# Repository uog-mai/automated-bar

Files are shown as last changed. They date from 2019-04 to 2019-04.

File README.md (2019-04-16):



 

<p align="center">
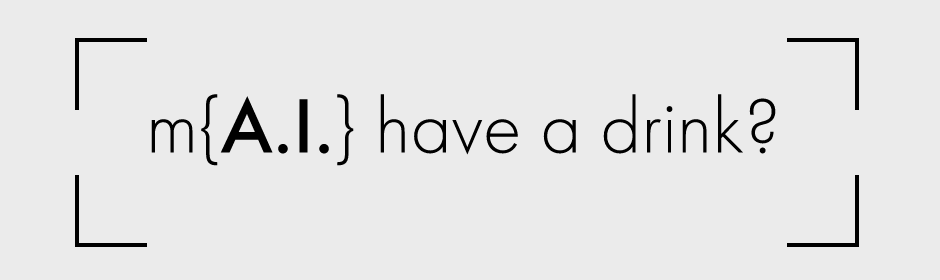
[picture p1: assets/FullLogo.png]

</p>

# m{A.I.} get you a drink?

m{A.I.} is a project aiming to produce a low-cost, voice-activated, automated drinks vending system for use in high-end consumer and commercial applications. Order your favourite drink through voice commands on Google Home on your mobile or use our custom made GUI to select drinks. 

This page will show you exactly how to build your own automated-bar for under £75, providing you with a components list, all the necessary CAD technical drawings and electronics schematics and an easy one step install for all the required software and firmware. 

Check out our design and build process on our Instagram page: [m{A.I.}.](https://www.instagram.com/m_a.i._/?hl=en)

Or our instructables for our full build instructions visit our [Instructables](https://www.instructables.com/id/Automated-Bar/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)

Completed as part of the University of Glasgow's Real Time Embedded Programming 5 team project

<p align="center">
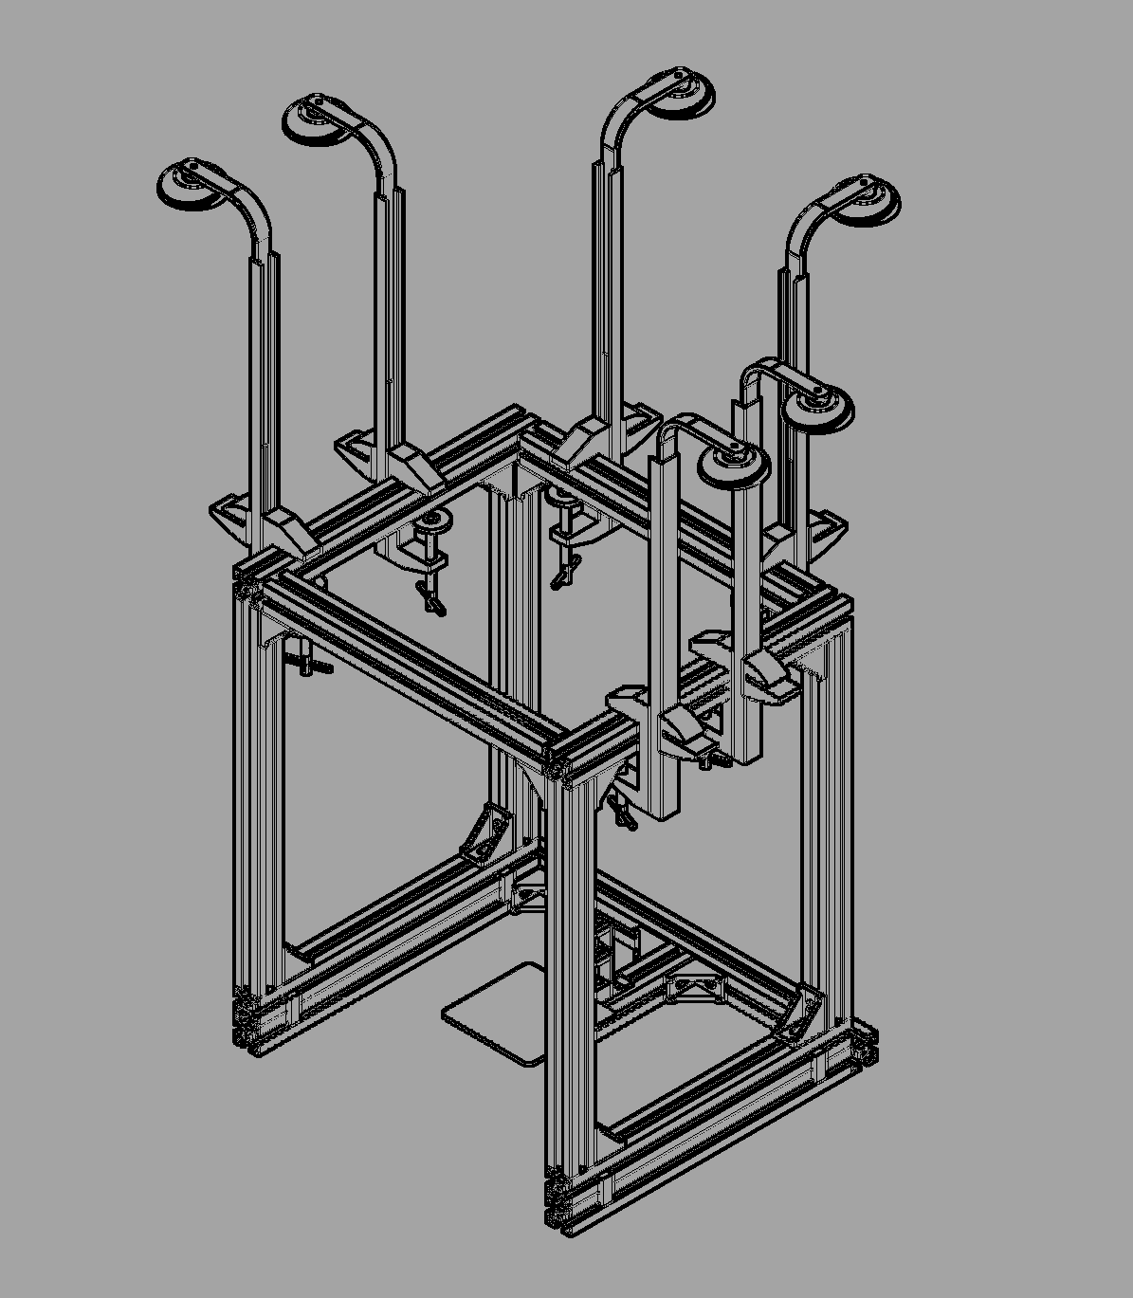
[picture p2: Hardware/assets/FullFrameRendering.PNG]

</p>

<p align="center">
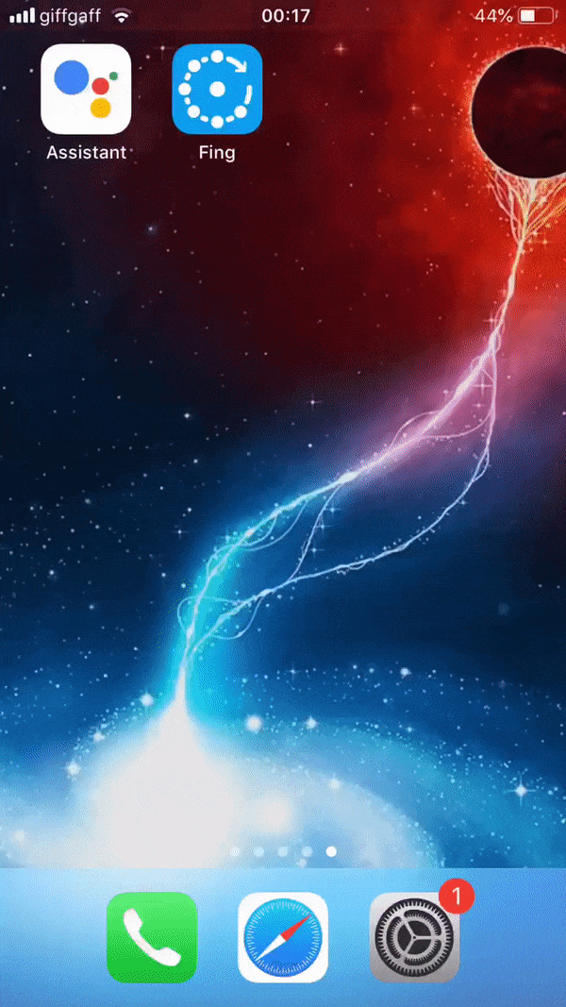
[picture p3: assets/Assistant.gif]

</p>
 
## Features
Scalability to any assortment of spirits and mixers

Google API integration for voice ordering

Extensive crawled database of recipes

Based on a Raspberry Pi 3 Model B

Low-cost aluminium extrusion structure

3D printed PLA fixtures

9g servo actuators

## Usage and Install Instructions
To use [dialogflow](https://dialogflow.com/) you must create a free account and import the ```CocktailRecipeBot``` which can be download from the software directory ```automated-bar/Software/dialogflow```. Download, unzip and upload it to dialogflow to begin use.

You will also need to sign-up and download [```ngrok```](https://dashboard.ngrok.com/user/signup) a secure traffic rerouting service for webhooks. This is needed to connect the dialogflow webhook to the Python server. This should be done on the Raspberry Pi.

This following software has only been verified to compile on the Raspberry Pi 3 Model B ```raspian (stretch)``` and ```Ubuntu 16.04```, however it should work on other raspbian distros and RPI models too.

This installation should be run from the command line of the Raspberry Pi by first cloning this git repo.
```bash
git clone https://github.com/uog-mai/automated-bar/
cd automated-bar/Software/
sudo source build.sh
```
This will download, install and compile all dependencies and the source code for the project.

Once installed, run the following in the ```ngrok``` install directory:
```bash
sudo ./ngrok http 5000
```
This will redirect a dynamically generated URL to your RPI. Where it says:
```Forwarding                    https://yourURL.ngrok.io``` copy the URL (makes sure its https *not* http). In the ``CocktailRecipeBot`` dialogflow on the left hand side where it says ```Fulfillment```, enable the webhook option and paste the ngrok URL.

Now navigate to the server folder inside the software directory, ```automated-bar/Software/Server``` and run:
```bash
python3 index.py
``` 
This should run your webserver (default traffic input through port 5000) on the RPI with the C++ shared object imported as a module. 

*Congratulations* You have completed the software set-up, you can now ask Google Home to talk to ```m{A.I.}``` (through voice or text) and you can begin ordering your drinks. 

## Overview
The automated bar holds an array of alcoholic drinks and mixers of the users choice, clamped onto the top of the frame, each paired with their own mounted servos. When a user orders a drink the volume and weight of the desired drink is found and calculated, and the appropriate servos are driven to dispsense the fluid the correct beverage. A proximity sensor on the cup stand checks whether a user has added a cup and a weight sensor confirms the correct amount of fluid has been dispensed. 

### Hardware 

#### Links

Full CAD resources including Autodesk Inventor files and assemblies of the system can be found within our Hardware subsection, and full electronics design files are available through the [Altium CircuitMaker community.](https://circuitmaker.com/Projects/Details/Peter-Fleming-2/UoG-mai-automated-bar) 

For full build instructions and BOM please see our Instructables page [here](https://www.instructables.com/id/Automated-Bar/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)

### Software
The software is split up into two sections: ```C++``` firmware and logic and and a ```Python``` web server that interacts with dialogflow. The logic section interacts with the firmware of the sensors and controls the handling of the fluid and the verificaiton of states. The Python web server acts to parse and network information from dialogflow to the logic.

<p align="center">
<img src="https://github.com/uog-mai/automated-bar/blob/develop/assets/InteractionDiagram.png" ">
</p>

Further details of the software can be found in the Software directory README: ```automated-bar/Software/README```and in the Software section of the Wiki.

## Contributors
[Peter Fleming](https://github.com/petemfleming)

[Joseph Marsden](https://github.com/jrmars)

[Edward Mortimer](https://github.com/eddymj96)

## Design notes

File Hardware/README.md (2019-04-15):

# Hardware Design

## Mechanical Build
The system was modelled in Autodesk Inventor Professional and comprised of aluminium extrusion and fixtures, COTS optics 
with rail mounts, and custom designed 3D printed PLA components. 
### Manufactured frame
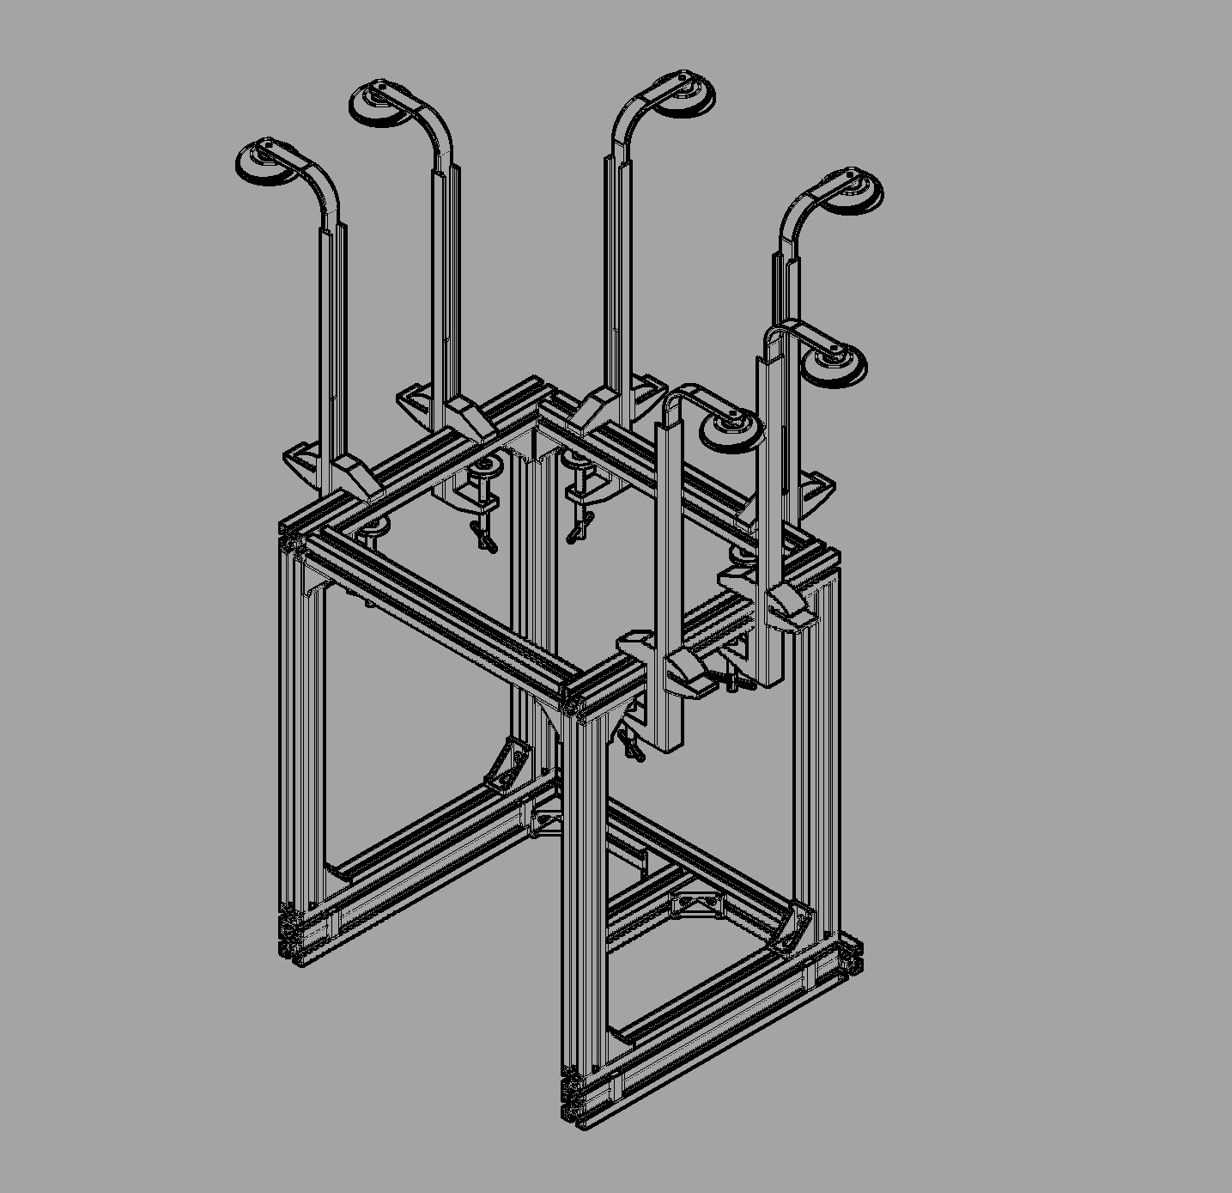
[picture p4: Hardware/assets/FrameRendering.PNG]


The dispensing systems operates through a 9g servo mounted on each optic, with a metal strut connecting it to the base of the 
plunger. As the servo rotates, the plunger mechanism is pulled upwards, closing the fill-line to the bottle, opening the 
dispenser line, and allowing air return via a sprung element within the optic.

### Optic dispensing assembly
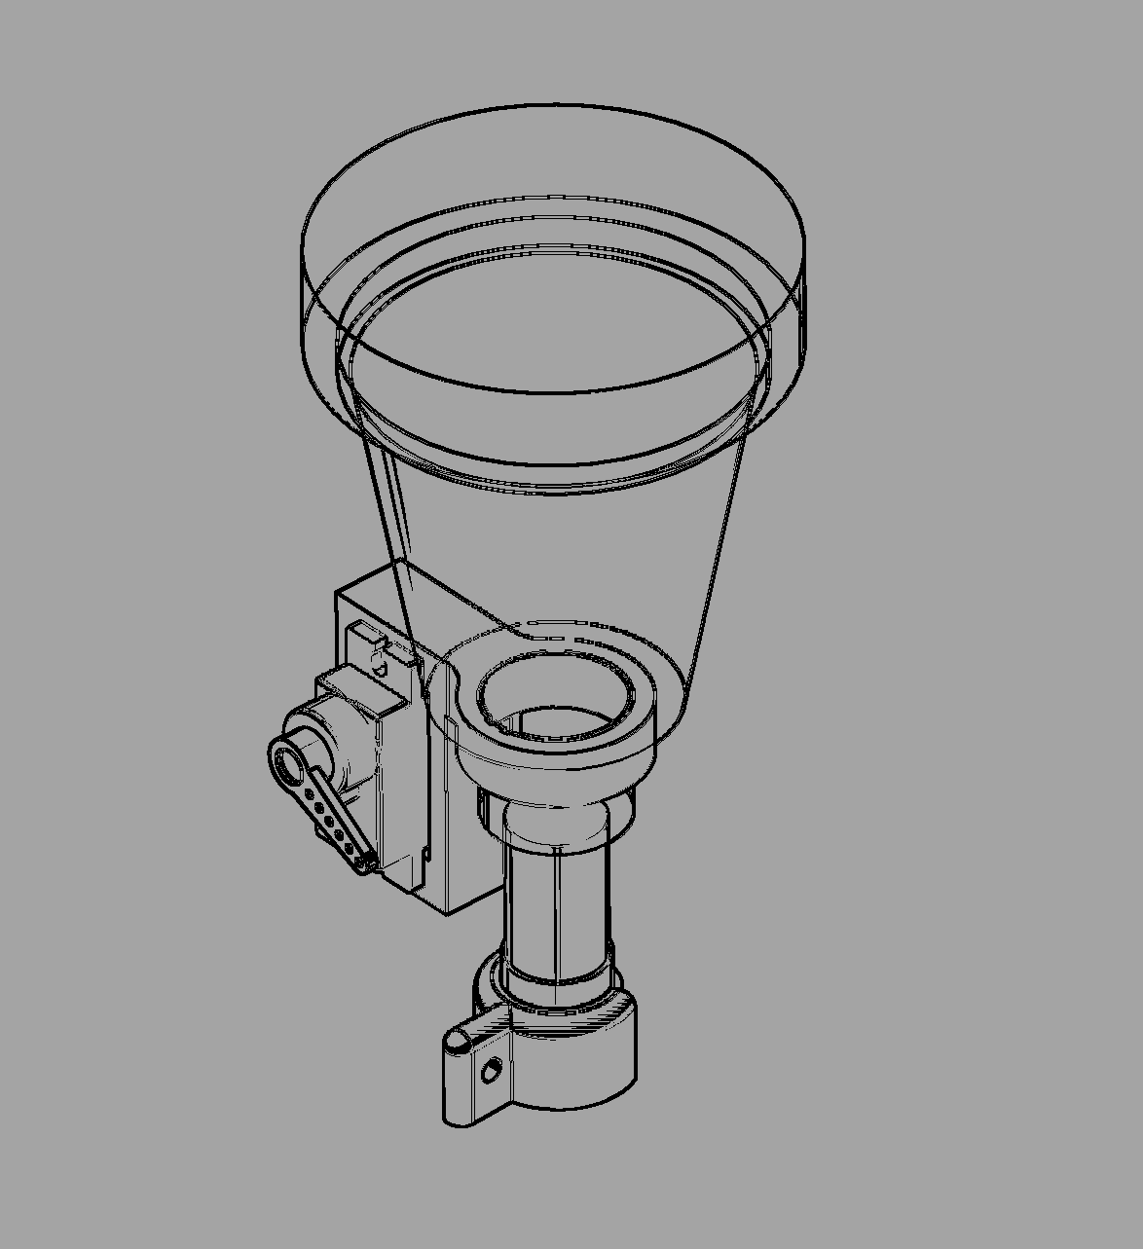
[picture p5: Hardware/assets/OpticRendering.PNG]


Food grade PVC tubes run from each optic and are held centrally above the receptacle by two aligning components.

### Dispenser alignment
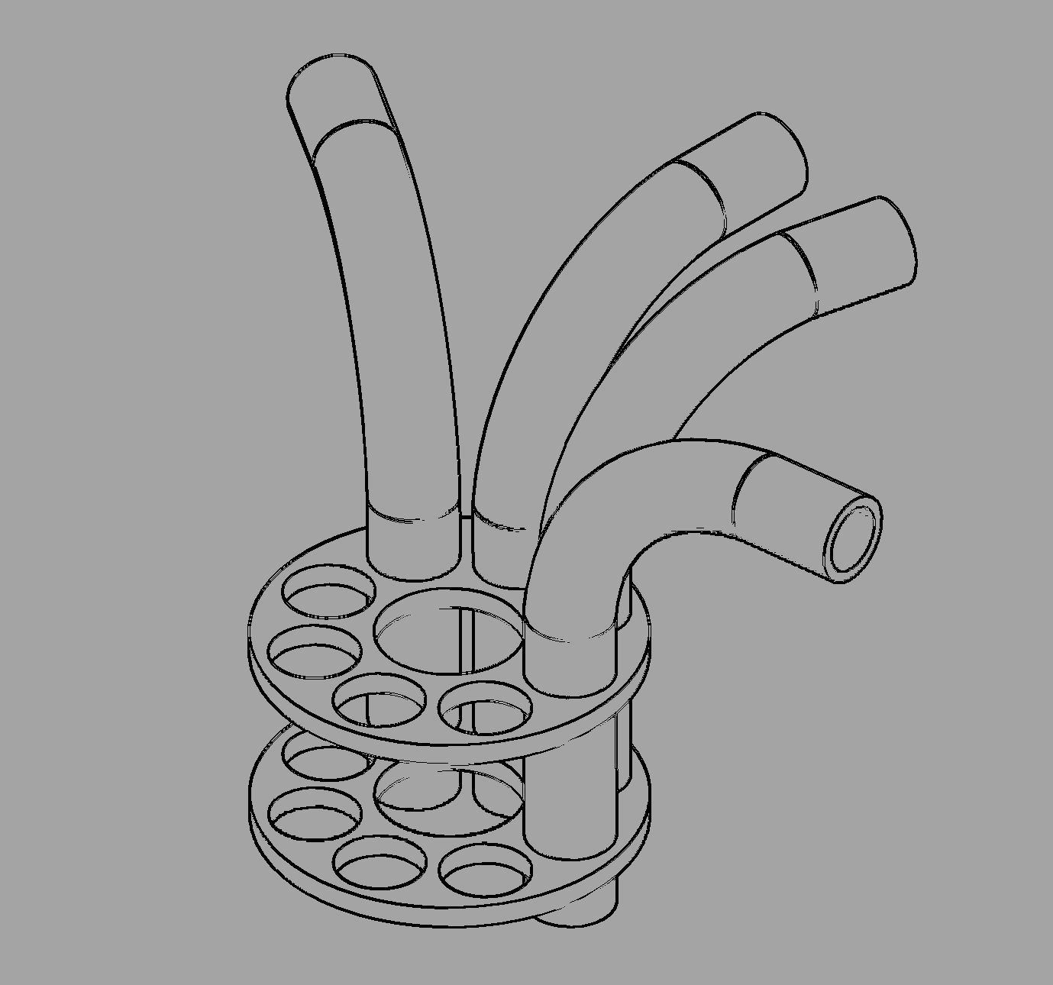
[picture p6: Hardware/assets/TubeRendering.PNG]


The user's drinking vessel is placed upon a carbon fiber plate, mounted to a load cell with a printed element. This is 
then rigidly mounted to the frame for feedback within the dispensing system.

### Loadcell baseplate
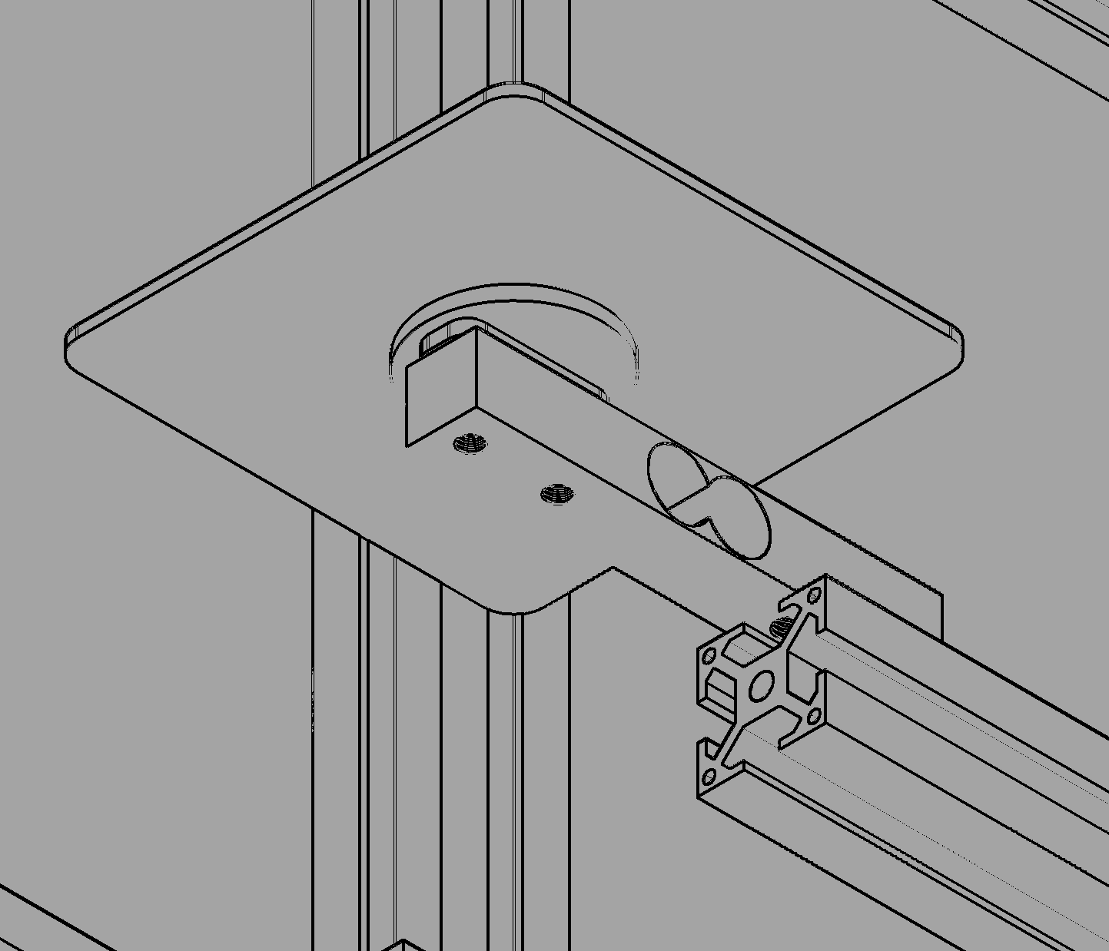
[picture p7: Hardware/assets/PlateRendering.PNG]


Behind this is a digital proximity sensor, providing detection of a cup on the plate, held in position by a sliding 
printed mounting on the extrusion.
###Proximity sensor mounting
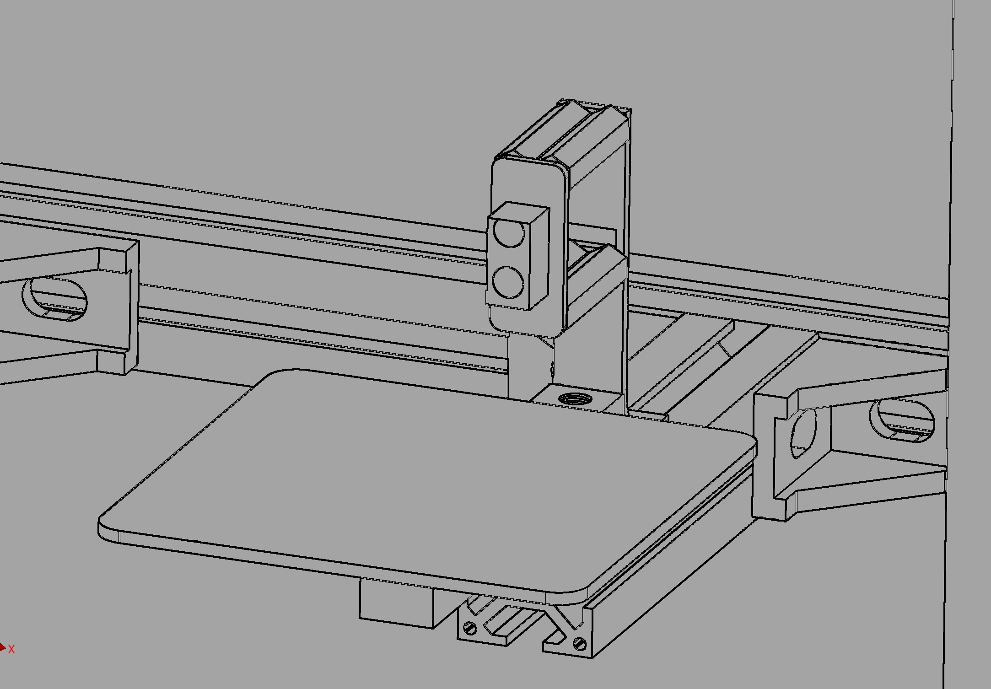
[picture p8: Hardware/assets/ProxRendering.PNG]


### Design files

Inventor parts and assembly files are provided, with additional STL models for printed components. Technical drawings 
for key parts are also included, and can also be derived from the inventor documents in mm scale. 

## Electronic Design
The system electronics were designed utilising Altium's CircuitMaker open-hardware designer. This package provides added 
functionality in ways of a community generated parts library integrated with the Octopart component database, aiding in 
speed of design and distributor oriented part selection and BOM generation. The main shield went through two revisions. 
An initial low quality test PCB created in house at the Univeristy of Glasgow featured the base servo control 
functionality, and aided in iterating the mechanical design.  The final board was designed to a higher specification and 
manufactured using JLCPCB's prototype PCB service.

### Final shield rendering
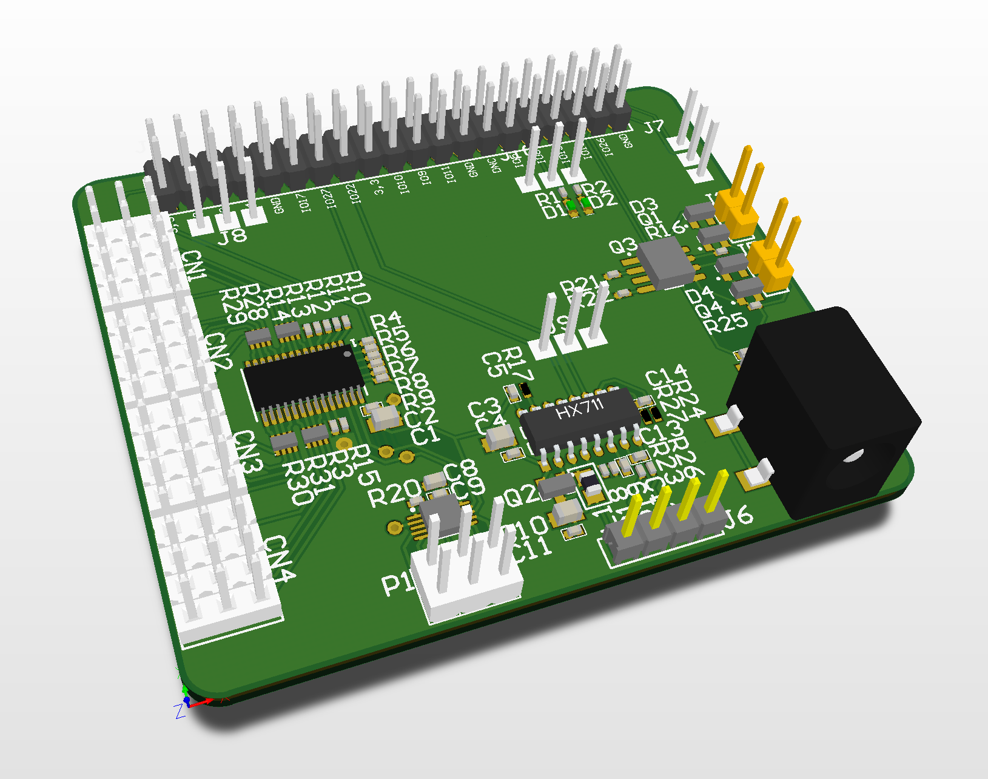
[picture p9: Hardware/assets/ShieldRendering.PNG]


The populated board provided the following core features:
* x8 Servo channels
* x1 Load cell amplifier input
* x1 Digital proximity sensor input
* x2 Debug GPIO pins with LEDs

For future development, pads were also provided for:
* x8 Additional servo channels
* x4 General purpose ADC inputs
* x1 Spare load cell amplifier channel
* x2 Opto-isolated solenoid drivers with 12V rail

### Proximity sensor board

An additional board was built to mount the digital proximity sensor and it's required circuitry, and can be built out of 
un-finished FR4 easily. Alternatively, several expansion boards are available for the same or similar ICs,  and the 
design utilised uses the same recommended schematic and layout design.

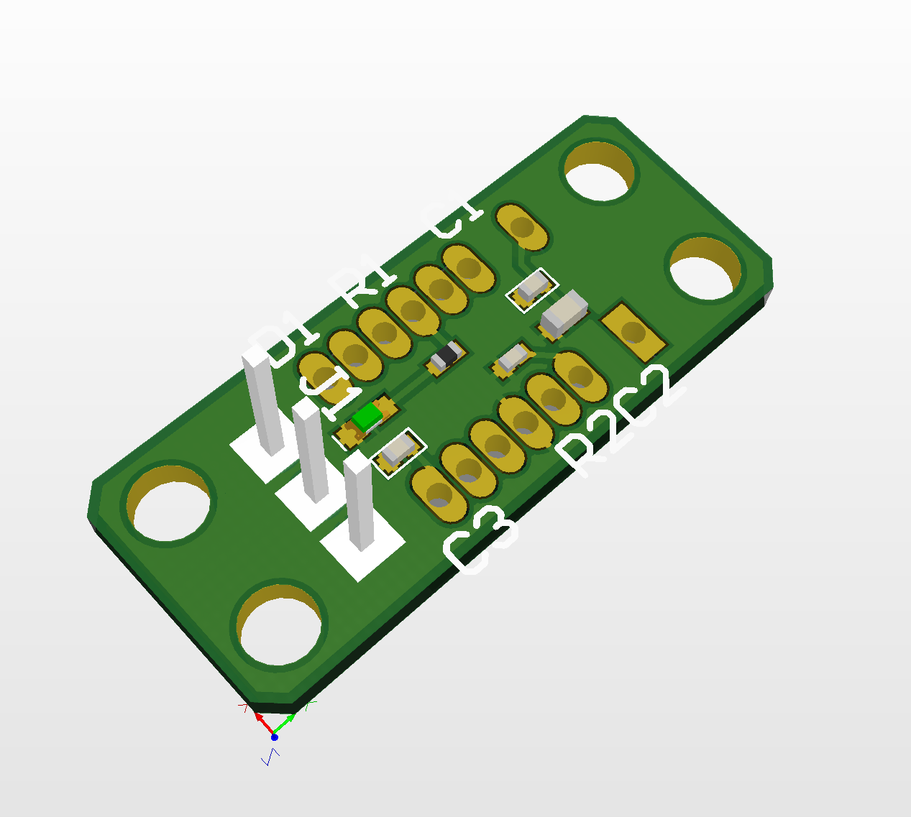
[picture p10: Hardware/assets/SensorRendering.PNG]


For full design files, see the publicly accessible CircuitMaker project: https://circuitmaker.com/Projects/Details/Peter-Fleming-2/UoG-mai-automated-bar

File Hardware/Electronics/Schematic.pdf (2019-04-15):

I2C -> PWM | R.PI HEADER

## DEBUG

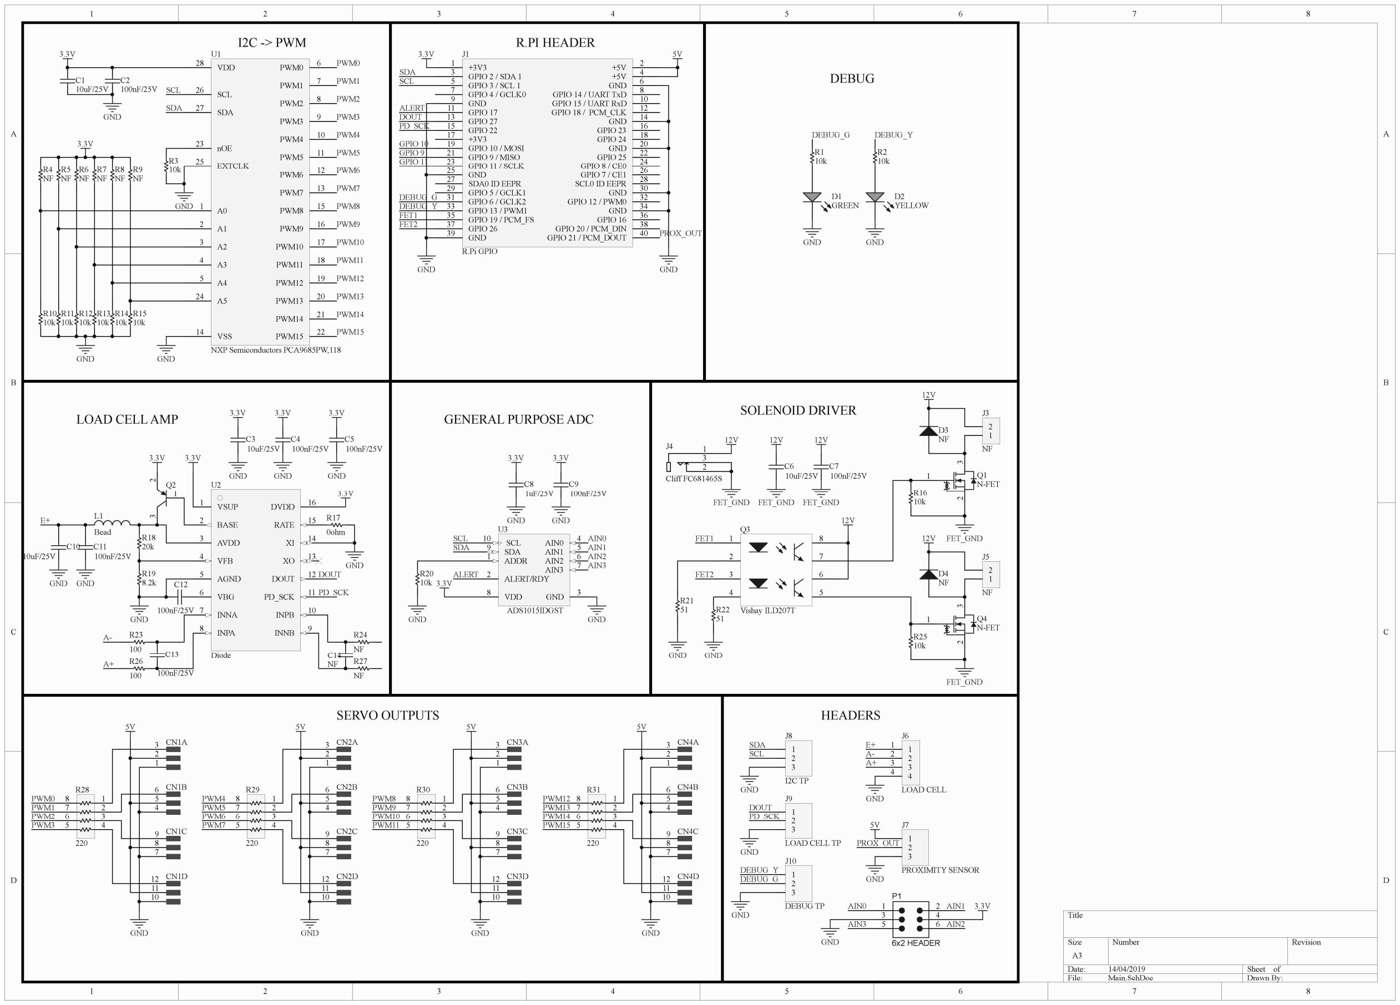
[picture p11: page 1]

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
Title

Size | Number | Revision
A3
Date: | 14/04/2019 | Sheet of
File: | Main.SchDoc | Drawn By:

A0 1

A1 2

A2 3

A3 4

A4 5

PWM0 | 6
PWM1 | 7
PWM2 | 8
PWM3 | 9
PWM4 | 10
PWM5 | 11
PWM6 | 12
PWM7 | 13

VSS 14

PWM8 | 15
PWM9 | 16
PWM10 | 17
PWM11 | 18
PWM12 | 19
PWM13 | 20
PWM14 | 21
PWM15 | 22

nOE 23

A5 24

EXTCLK 25

SCL 26

SDA 27

VDD 28

U1

NXP Semiconductors PCA9685PW,118

PWM0

PWM1

PWM2

PWM3

PWM4

PWM5

PWM6

PWM7

PWM8

PWM9

PWM10

PWM11

PWM12

PWM13

PWM14

PWM15

3.3V

GND

SCL

SDA

GND

+3V3 1 | +5V | 2
GPIO 2 / SDA 1 3 | +5V | 4
GPIO 3 / SCL 1 5 | GND | 6
GPIO 4 / GCLK0 7 | GPIO 14 / UART TxD | 8
GND 9 | GPIO 15 / UART RxD | 10
GPIO 17 11 | GPIO 18 / PCM_CLK | 12
GPIO 27 13 | GND | 14
GPIO 22 15 | GPIO 23 | 16
+3V3 17 | GPIO 24 | 18
GPIO 10 / MOSI 19 | GND | 20
GPIO 9 / MISO 21 | GPIO 25 | 22
GPIO 11 / SCLK 23 | GPIO 8 / CE0 | 24
GND 25 | GPIO 7 / CE1 | 26
SDA0 ID EEPR 27 | SCL0 ID EEPR | 28
GPIO 5 / GCLK1 29 | GND | 30
GPIO 6 / GCLK2 31 | GPIO 12 / PWM0 | 32
GPIO 13 / PWM1 33 | GND | 34
GPIO 19 / PCM_FS 35 | GPIO 16 | 36
GPIO 26 37 | GPIO 20 / PCM_DIN | 38
GND 39 | GPIO 21 / PCM_DOUT | 40

J1

R.Pi GPIO

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
10uF/25V

C2
100nF/25V

GND

1

2

### 3 CN1A

4

5

### 6 CN1B

7

8

### 9 CN1C

10

11

### 12 CN1D

5V

GND

1

2

### 3 CN2A

4

5

### 6 CN2B

7

8

### 9 CN2C

10

11

### 12 CN2D

5V

GND

PWM0
PWM1
PWM2
PWM3

PWM4
PWM5
PWM6
PWM7

1

2

### 3 CN3A

4

5

### 6 CN3B

7

8

### 9 CN3C

10

11

### 12 CN3D

5V

GND

1

2

### 3 CN4A

4

5

### 6 CN4B

7

8

### 9 CN4C

10

11

### 12 CN4D

5V

GND

PWM8
PWM9
PWM10
PWM11

PWM12
PWM13
PWM14
PWM15

D1
GREEN

R1
10k

R2
10k
GND | GND

GPIO 10
GPIO 9
GPIO 11

FET2

FET1

DEBUG_G DEBUG_Y

## SERVO OUTPUTS

D2
YELLOW

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
VSUP 1

BASE 2

AVDD 3

VFB 4

AGND 5

VBG 6

INNA 7

INPA 8

DVDD | 16
RATE | 15
XI | 14
XO | 13
DOUT | 12
PD_SCK | 11
INPB | 10
INNB | 9

U2

Diode

### 1 ² 3

Q2

PD_SCK

DOUT

GND

GND
R23
100
R26
100

C13

100nF/25V

C12

100nF/25V

R19
8.2k

R18
20k

L1
Bead
C10
10uF/25V

C11
100nF/25V

GND

A-

A+

GND

C3
10uF/25V

C4
100nF/25V

GND GND

E+

3.3V

C5
100nF/25V

GND

3.3V

R17
0ohm

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
LOAD CELL

E+

A+

A-

GND

## LOAD CELL AMP

ADDR 1

ALERT/RDY 2

GND | 3
AIN0 | 4
AIN1 | 5
AIN2 | 6
AIN3 | 7

VDD 8

SDA 9

SCL 10

U3

ADS1015IDGST

1
2
3

J7

PROXIMITY SENSOR

5V

GND

PROX_OUT

ALERT

GND

R20
10k

GND

AIN0
AIN1
AIN2
AIN3

C9
100nF/25V

GND

C8
1uF/25V

GND

AIN3

1 | 2 3 | Q1
| | N-FET

1

2

J3

### 1 NF

3
2

J4

Cliff FC681465S

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
Vishay ILD207T

GND

12V

FET_GND

D3
NF

R16
10k
1 | 2 3 | Q4
| | N-FET

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
100nF/25V
12V | 12V

FET_GND

FET_GND

FET_GND FET_GND

12V

12V

12V

FET1

FET2

R21

### 51 R22

51

GND

## SOLENOID DRIVER GENERAL PURPOSE ADC

1 2
3 4
5 6

P1

6x2 HEADER

## HEADERS

DEBUG_G
DEBUG_Y

ALERT
DOUT
PD_SCK

SCL
SDA

C6
10uF/25V
AIN0 | AIN1
| AIN2

GND

1
2
3

J8

I2C TP

1
2
3

J10

DEBUG TP

GND

SCL

SDA

DEBUG_G

DEBUG_Y

GND

1
2
3

J9

LOAD CELL TP

PD_SCK

DOUT

GND

PROX_OUT

GND | GND

3.3V

3.3V

3.3V | 3.3V

3.3V

3.3V

3.3V | 3.3V
3.3V | 3.3V

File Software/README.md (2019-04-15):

# Software
## Structure
The software consisists of two main sections: the server and the firmware. Firmware is the c++ source code that compiles to a shared object that contains the automated bar logic and interacts with the load cell (HX711), servos and proximity sensor. The server directory contains the a python web server that imports the shared object as a module, once it recieves a webhook from dialogflow it subsequently parses and accesses the desired behaviour through the binding.
```bash
.
|
|
├── build.sh
├── Firmware
│   ├── build
│   ├── CMakeLists.txt
│   ├── dependencies.sh
│   ├── include
│   ├── lib
│   ├── src
│   └── test
├── README.md
└── Server
    ├── database.py
    ├── index.py
    ├── __pycache__
    └── README.md
```
### Firmware

```build.sh```  is a bash script that automatically downlaods, installs and compiles the entire project on a RaspberryPi  model 3 B with raspian (stretch), it has also been verified to compile on Ubuntu 16.04 (However you wont be able to run it since you have no GPIO pins). This file calls the ```dependencies``` bash script which clones and isntalls the ```WiringPi``` and ```pca9685``` libraries. It also installs ```Python3```and ```pybind11``` a c++ --> python binding module. 

```include``` contains the c++ header files which are added during compilation.

```lib``` contains the external library source files that are not already installed for compilation.

```src``` contains the ```cpp``` source code which defines all the bar logic and behaviour.

``` test``` contains the unit tests which are automatically performed during compilation time.

### Server
```index.py``` is the Python file that uses ```Flask``` import modules to run as a web server. It recieves the webhook from dialogflow, parses the input and refers to the ```database.py``` Python script which contains methods and data that allows the server to retrieve the necessary densities of drinks and to provide a response to the user.

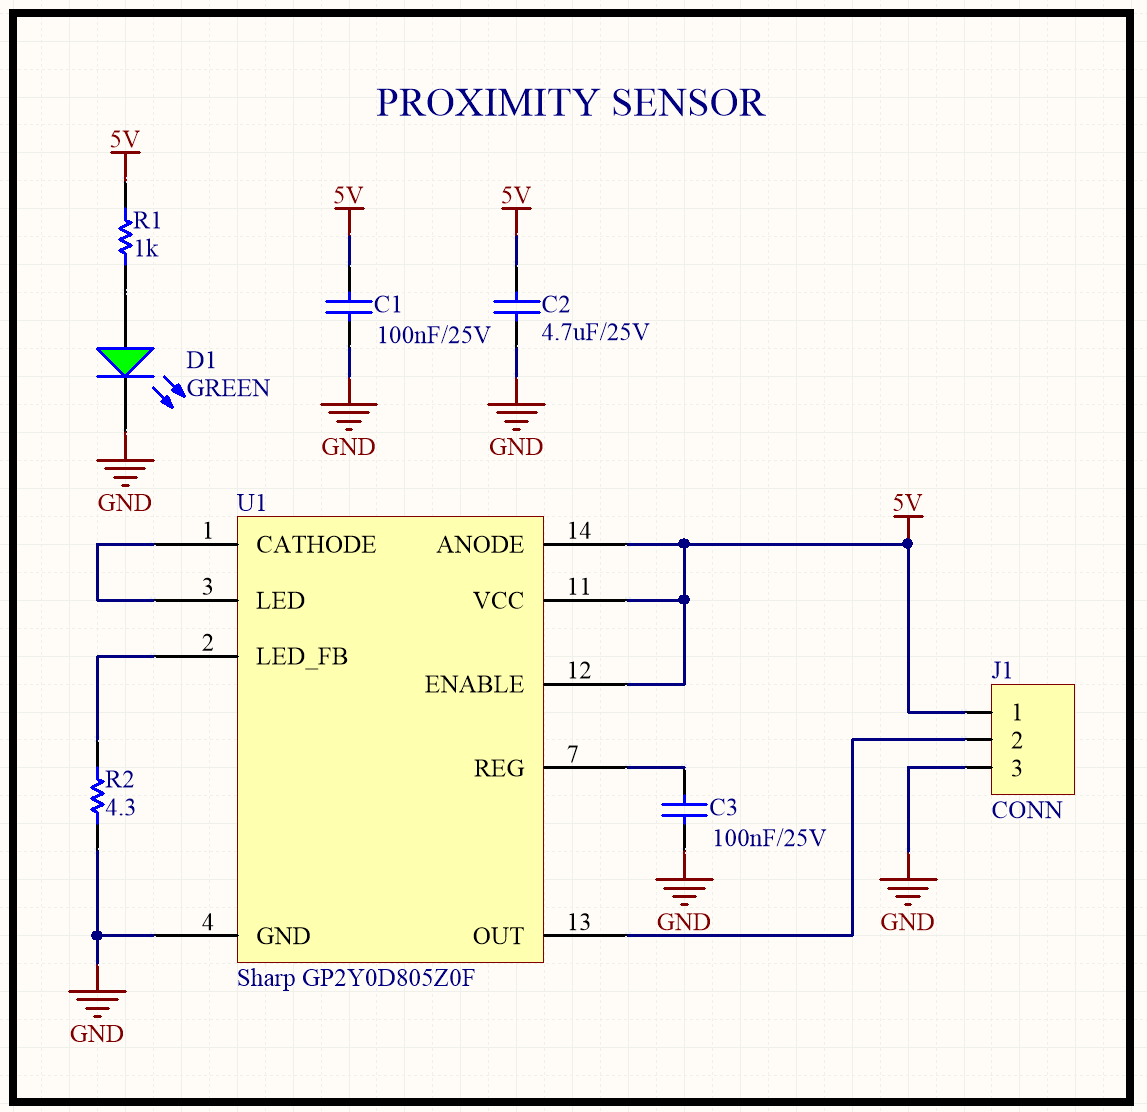
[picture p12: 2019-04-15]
Hardware/assets/SensorSchematic.PNG

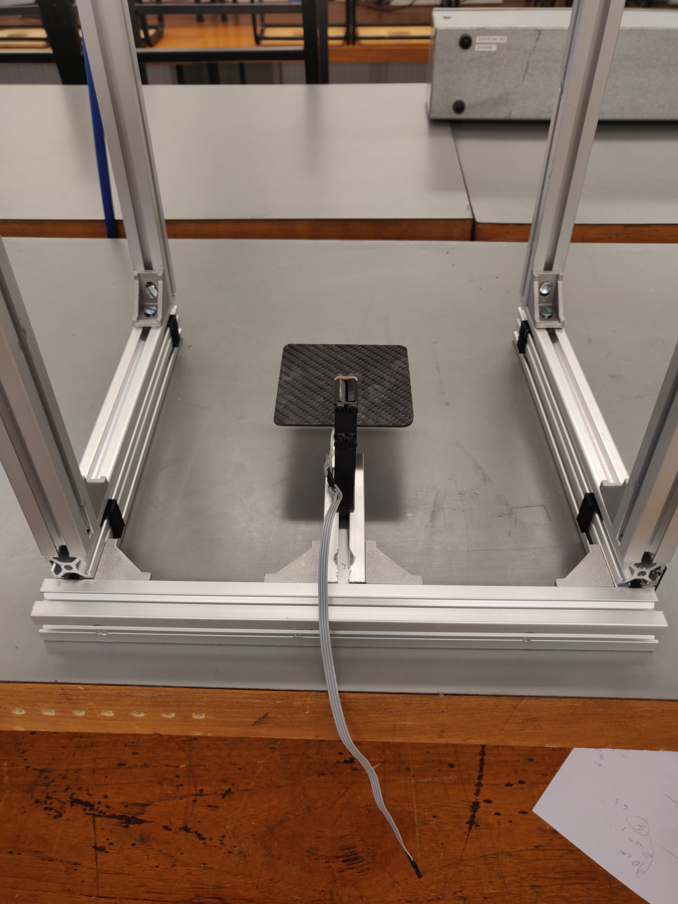
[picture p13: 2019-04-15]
Hardware/assets/FrameBack.jpg

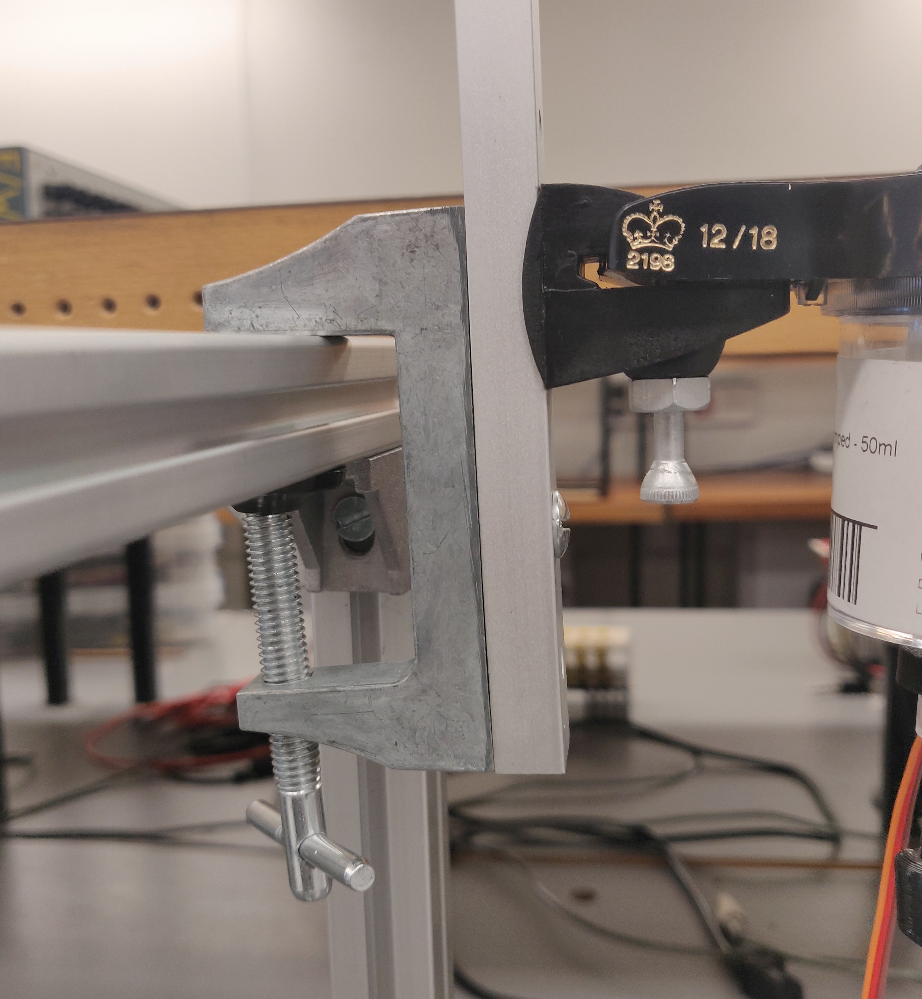
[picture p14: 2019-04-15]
Hardware/assets/Clamp.jpg

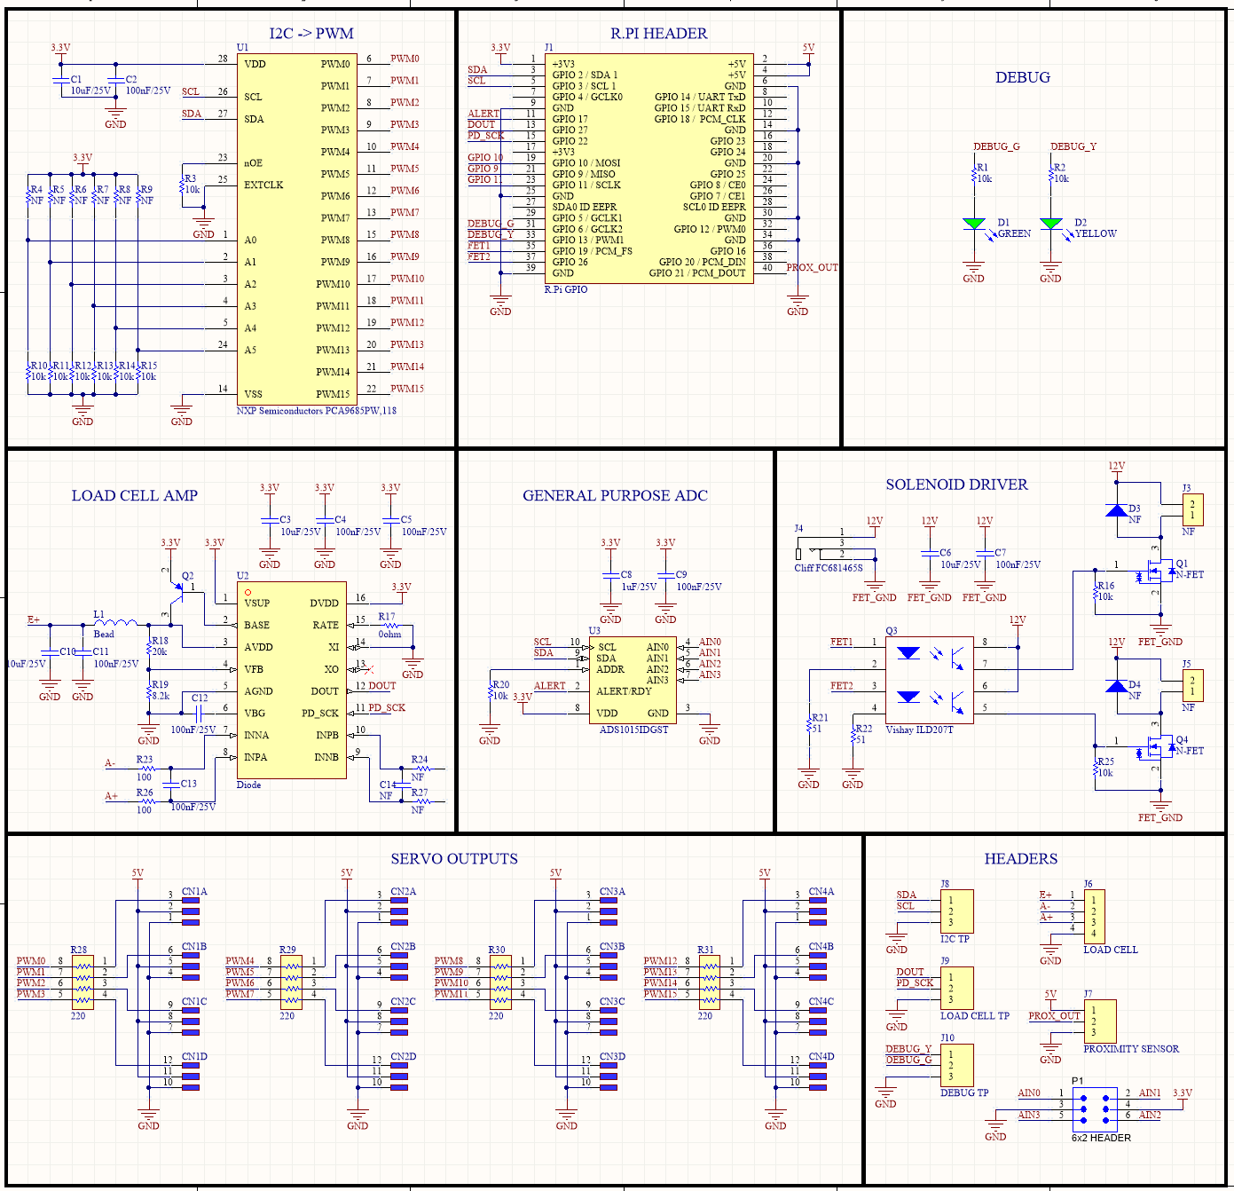
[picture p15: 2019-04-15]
Hardware/assets/ShieldSchematic.PNG

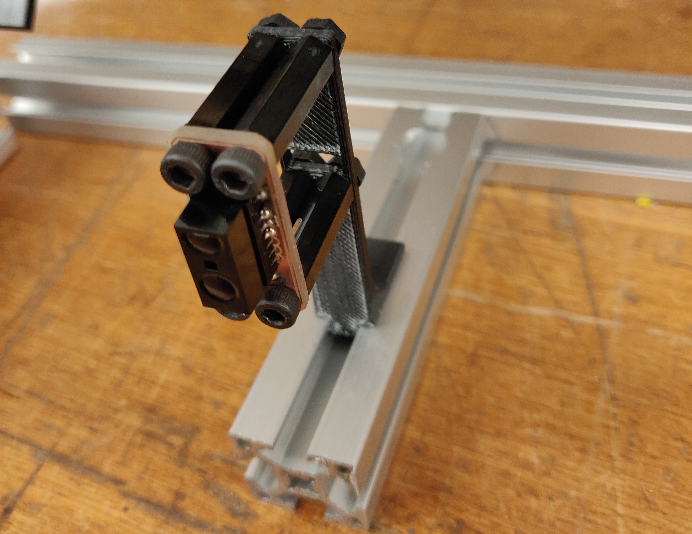
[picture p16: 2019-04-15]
Hardware/assets/Proximity.jpg

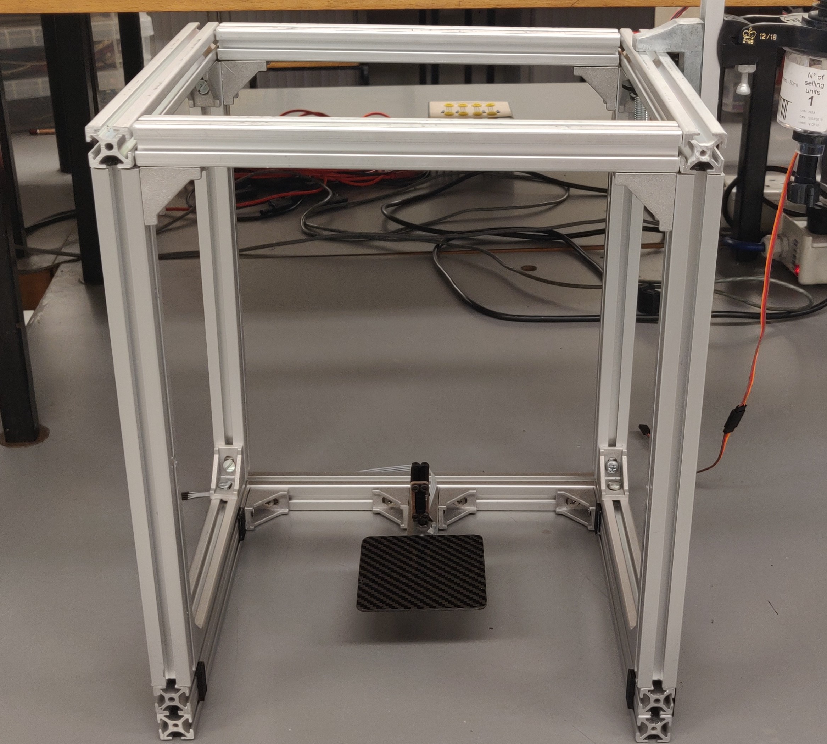
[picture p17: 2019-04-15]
Hardware/assets/FrameFront.jpg

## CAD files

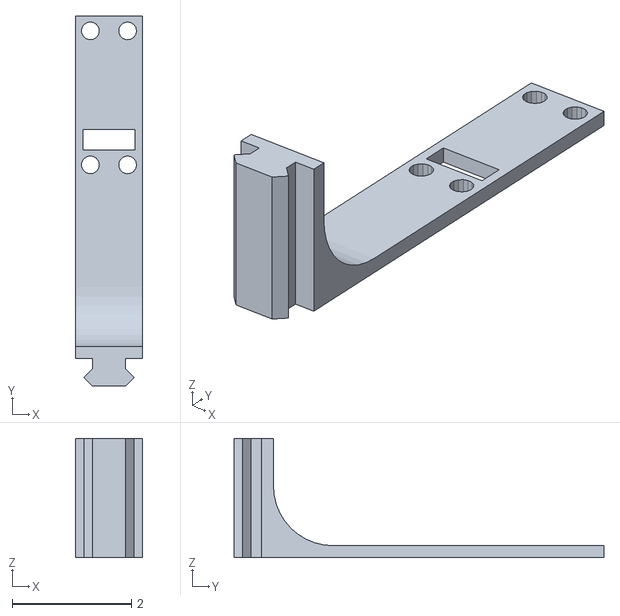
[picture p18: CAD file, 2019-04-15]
Hardware/CAD/STL print files/prox_base.stl
1.12 x 6.21 x 2.00

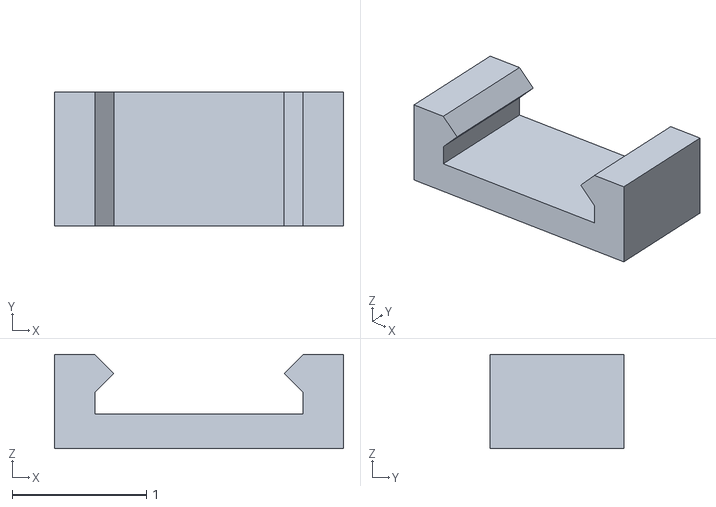
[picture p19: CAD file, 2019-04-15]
Hardware/CAD/STL print files/extrusion_clip.stl
2.15 x 1.00 x 0.7

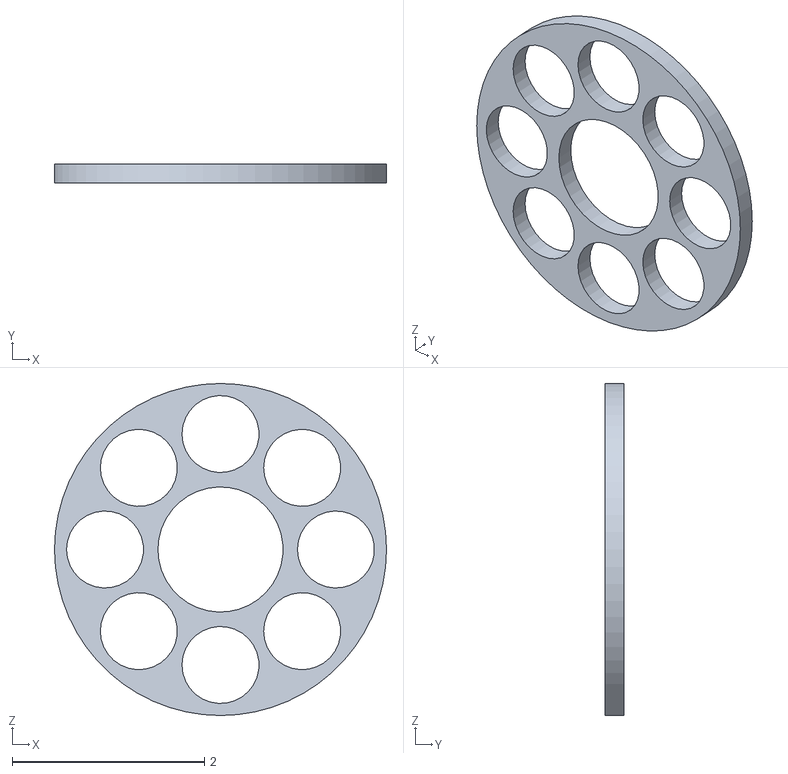
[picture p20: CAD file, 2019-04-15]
Hardware/CAD/STL print files/tube_clamp.stl
3.45 x 0.2 x 3.45

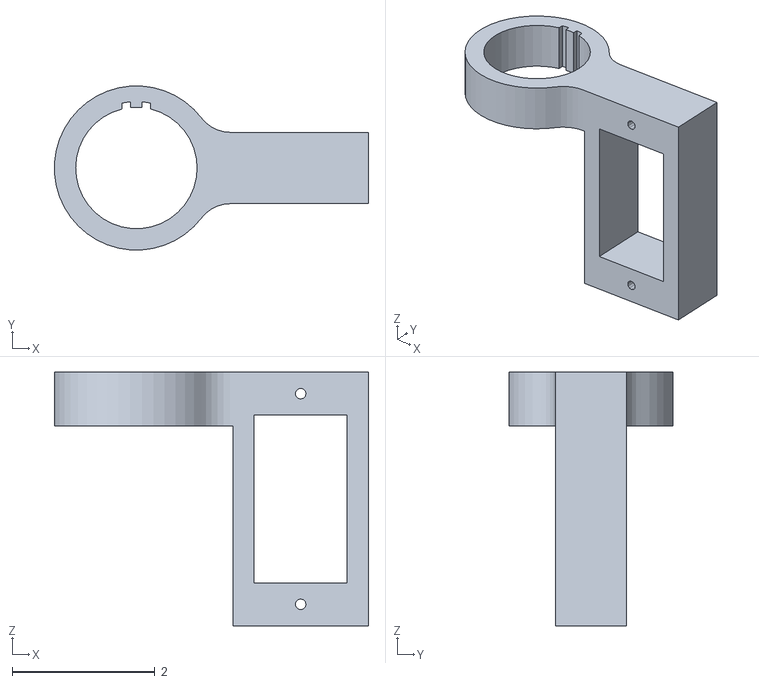
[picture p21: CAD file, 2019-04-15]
Hardware/CAD/STL print files/servo.stl
4.40 x 2.30 x 3.55

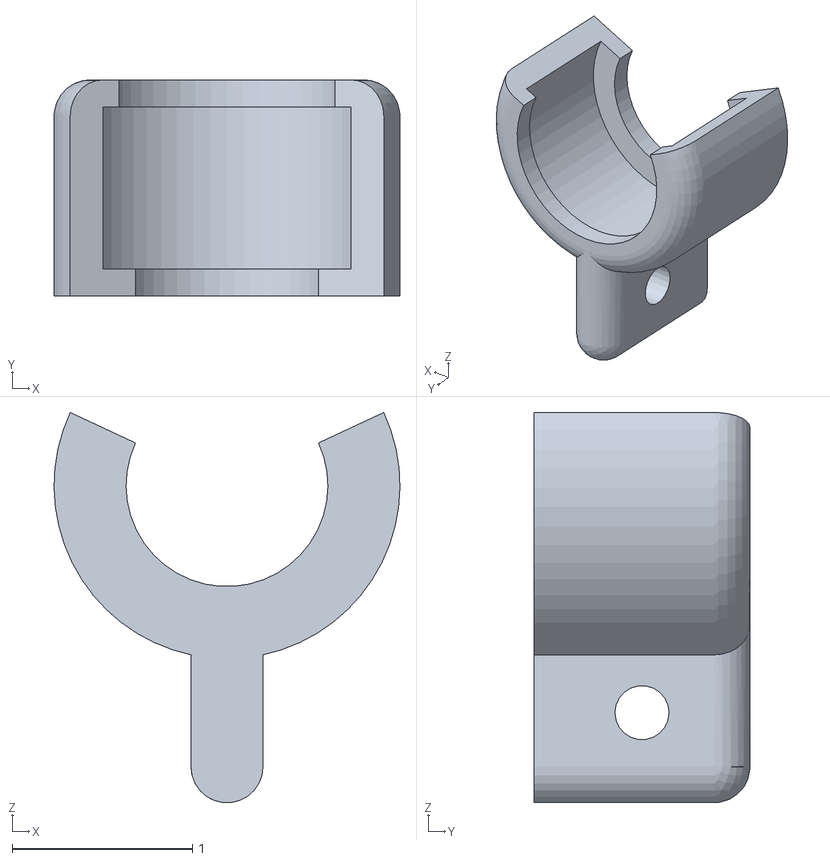
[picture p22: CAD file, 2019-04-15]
Hardware/CAD/STL print files/plunger.stl
1.92 x 1.20 x 2.16

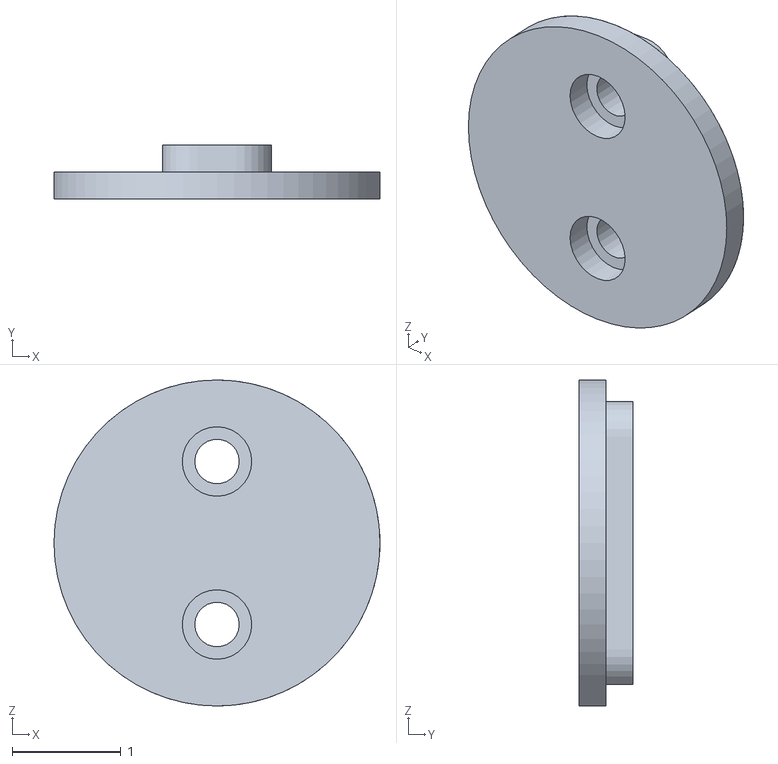
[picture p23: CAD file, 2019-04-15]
Hardware/CAD/STL print files/baseplate.stl
3.00 x 0.5 x 3.00

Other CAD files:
Hardware/CAD/IPT Inventor files/servo mount.dwg
Hardware/CAD/IPT Inventor files/baseplate.ipt
Hardware/CAD/IPT Inventor files/bracket.ipt
Hardware/CAD/IPT Inventor files/clamp.ipt
Hardware/CAD/IPT Inventor files/clamp_cup.ipt
Hardware/CAD/IPT Inventor files/cup.ipt
Hardware/CAD/IPT Inventor files/extrusion_250.ipt
Hardware/CAD/IPT Inventor files/extrusion_300.ipt
Hardware/CAD/IPT Inventor files/extrusion_95.ipt
Hardware/CAD/IPT Inventor files/extrusion_clip.ipt
Hardware/CAD/IPT Inventor files/frame.iam
Hardware/CAD/IPT Inventor files/mainbar.ipt
Hardware/CAD/IPT Inventor files/optic_rail.iam
Hardware/CAD/IPT Inventor files/opticmount.ipt
Hardware/CAD/IPT Inventor files/plunger.ipt
Hardware/CAD/IPT Inventor files/prox_base.ipt
Hardware/CAD/IPT Inventor files/screw.ipt
Hardware/CAD/IPT Inventor files/servo.ipt
Hardware/CAD/IPT Inventor files/topbar.ipt
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

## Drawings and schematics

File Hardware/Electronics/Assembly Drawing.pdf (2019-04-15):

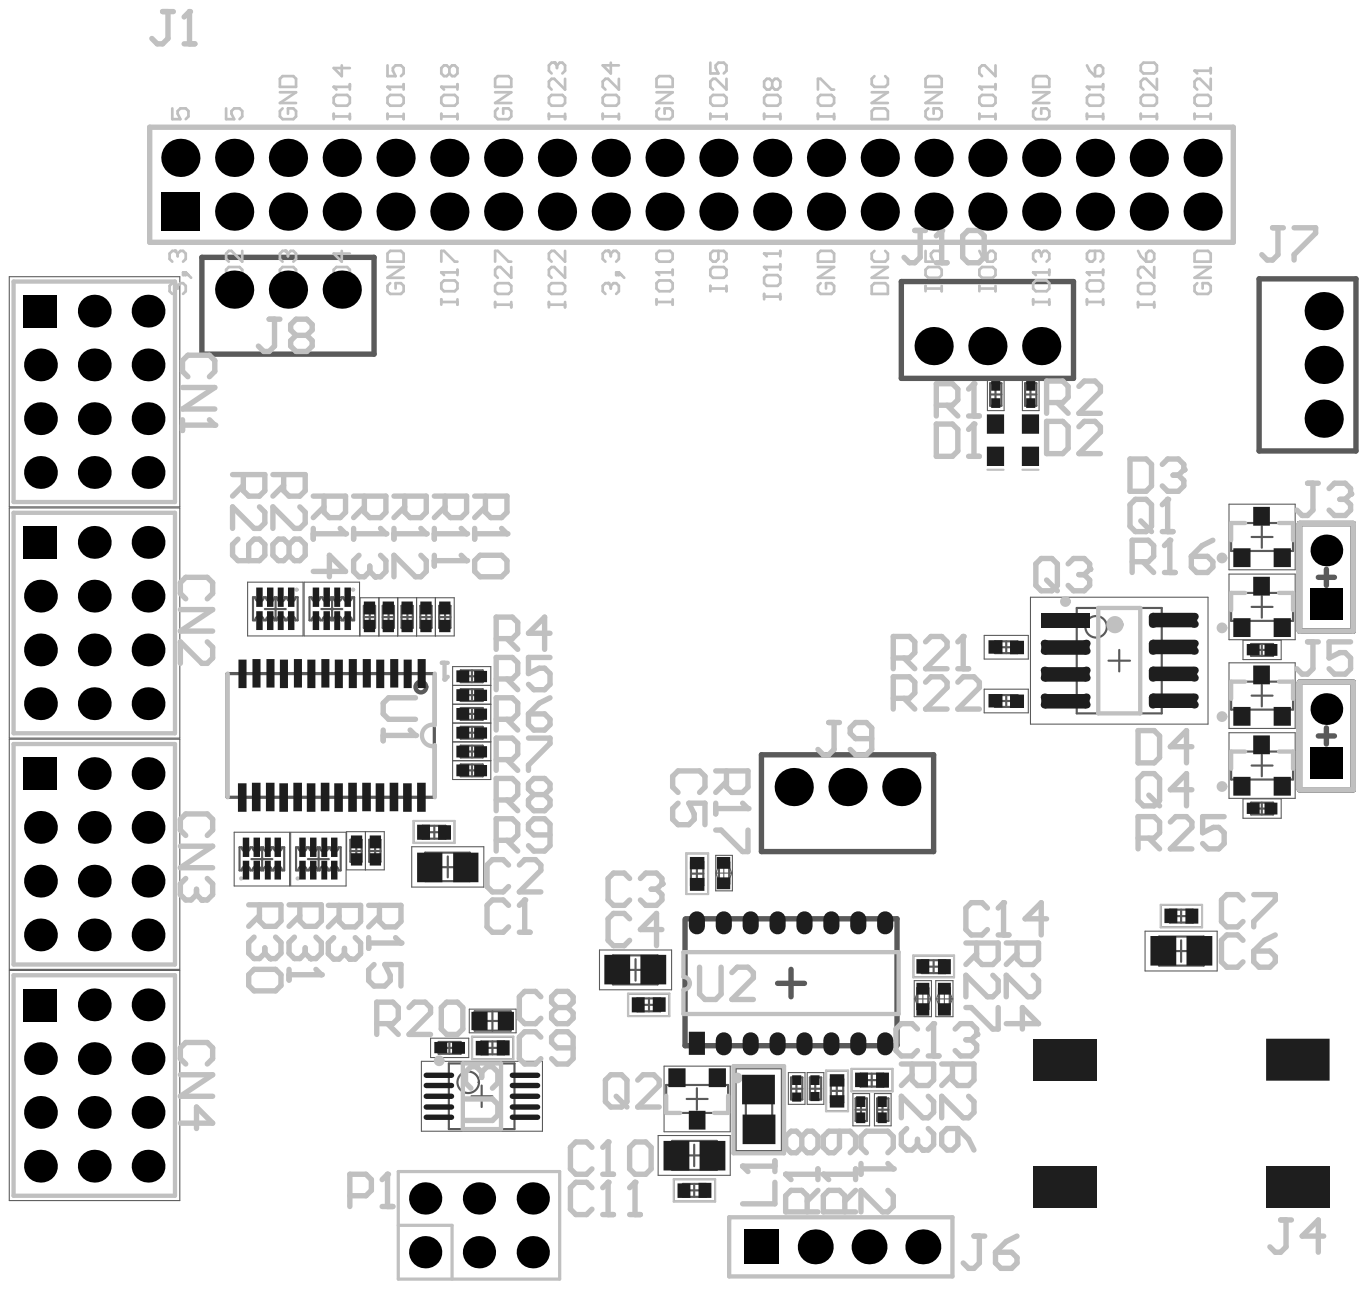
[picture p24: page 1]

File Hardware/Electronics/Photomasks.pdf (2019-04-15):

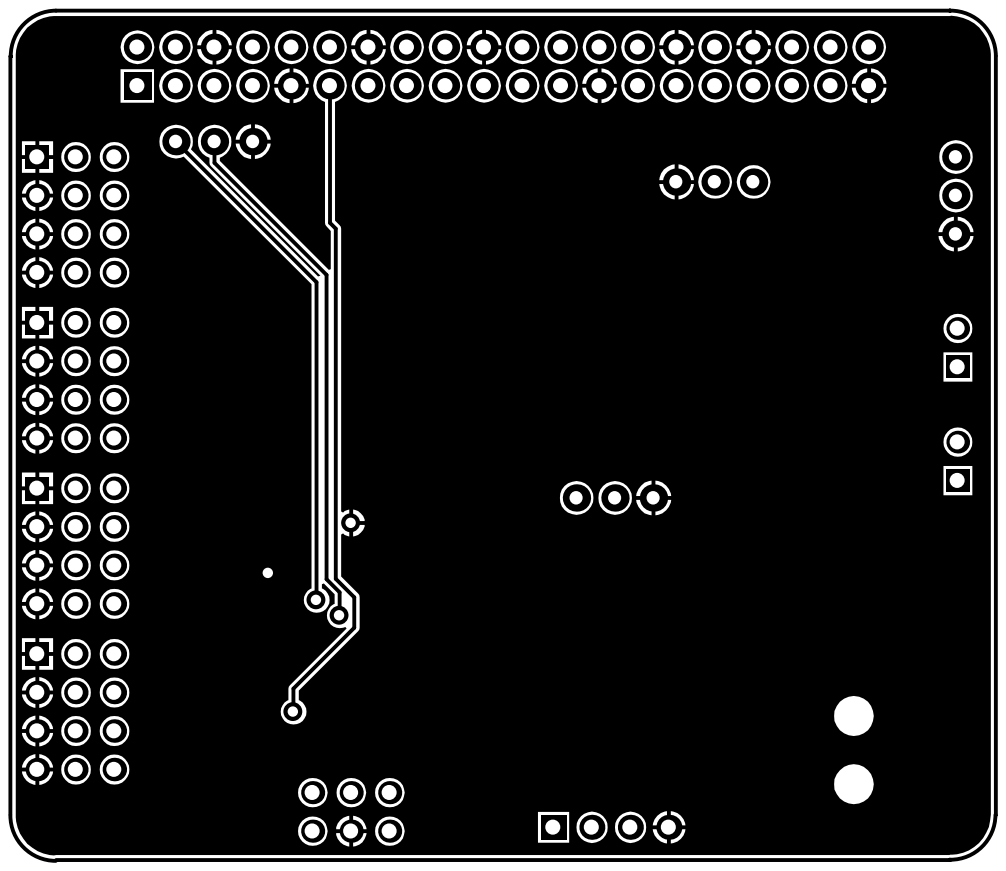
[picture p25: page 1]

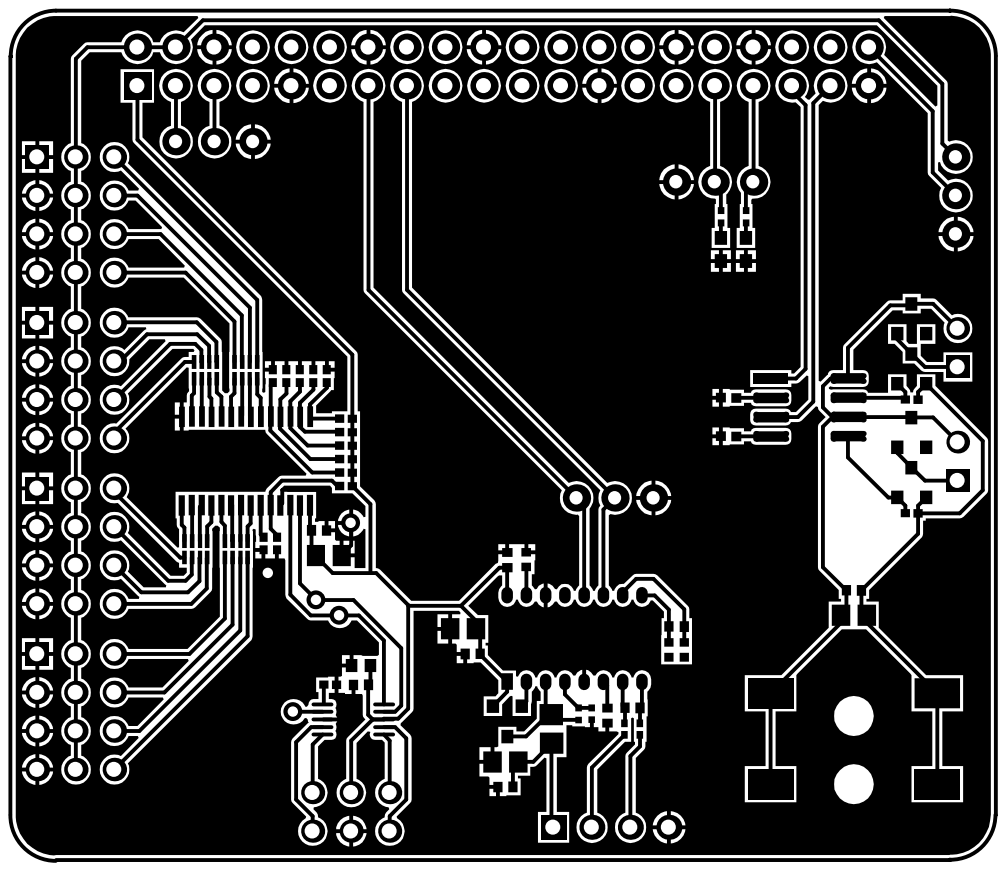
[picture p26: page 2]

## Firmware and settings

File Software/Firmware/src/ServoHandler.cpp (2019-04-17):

#include "ServoHandler.h"
#include "pca9685/src/pca9685.h"
#include <wiringPi.h>
#include <wiringPiI2C.h>
#include <stdexcept>
#include <cstdio>

ServoHandler::ServoHandler(const int pin_num)
                          : m_activated(false),
                            m_pin_num(pin_num) {

  /* Check the GPIO Pins are Setup. 
 if (WiringPiSetupGpio() == -1)
    throw std::runtime_error("Failed to setup GPIO for wiringPi");
*
  const int pca_setup = pca9685Setup(m_pin_base, 0x40, m_freq);

  if (pca_setup == -1);
    throw std::runtime_error("Failed to setup GPIO for wiringPiPca9685");
  
  
  pca9685PWMReset(pca_setup);
  */
  pinMode(m_RPI_pwm_pin, PWM_OUTPUT);
  pwmSetMode(PWM_MODE_MS);
  pwmSetClock(m_clockValue);
  pwmSetRange(m_rangeValue);
  

}

ServoHandler::ServoStatus ServoHandler::activate() {
    /* @TODO */
    m_activated = true;
    pwmWrite(m_pin_base + m_pin_num , m_pwm_on);
    printf("Servo Activated \n\n");
    return ServoHandler::ServoStatus::ACTION_SUCCESS;
}

ServoHandler::ServoStatus ServoHandler::deactivate() {
    /* @TODO */
    m_activated = false;
    pwmWrite(m_pin_base + m_pin_num , m_pwm_off);
    printf("Servo Deactivated \n\n");
    return ServoHandler::ServoStatus::ACTION_SUCCESS;
}

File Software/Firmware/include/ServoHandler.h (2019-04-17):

#pragma once

class ServoHandler {
public:

    enum class ServoStatus {
        ACTION_FAILURE,
        ACTION_SUCCESS
    };

    ServoHandler(const int pin_num);
    
    ServoStatus activate();

    ServoStatus deactivate();

private:

    bool m_activated;
    const unsigned int m_pin_num;
    const unsigned int m_RPI_pwm_pin = 18;
    const unsigned int m_clockValue = 192;
    //const unsigned int m_freq = 50;
    const unsigned int m_max_pwm = -1;
    const unsigned int m_pin_base = 300;
    const unsigned int m_rangeValue = 2000;
    const unsigned int m_pwm_on = 1000;
    const unsigned int m_pwm_off = 5;

};

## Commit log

2019-02-20 Simple script that connects to a servo and alternates a PWM output signal
2019-02-20 Added a servo controlling script
2019-02-21 Adding RPI servo setup and test
2019-03-29 Added Flask Python web server file 'index.py'; has to be run with ngrok. Also added the c++ python servo controlling script MultiServoCOntroller.cpp', this is compiled to a Python extension module 'e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
2019-04-05 Load-cell is now working, it also filter values for outliers to remove offset errors and averaging errors
2019-04-13 Added all but one src file for compilation and fixed subsequent compilation errors
    [DrinkServer.cpp, ServoHandler.cpp]
2019-04-14 cad files added to hardware branch
    [baseplate.ipt, baseplate.stl, extrusion_clip.ipt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]
2019-04-14 CAD files added to hardware subsection
2019-04-14 Fixed compilation of full source code
    [DrinkServer.cpp]
2019-04-14 Electronics resources added to hardware subsection
    [baseplate.ipt, baseplate.stl, extrusion_clip.ipt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]
2019-04-14 Build test
    [baseplate.ipt, baseplate.stl, extrusion_clip.ipt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]
2019-04-14 Hardware ReadMe finalised
    [bracket.ipt, clamp.ipt, clamp_cup.ipt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]
2019-04-15 Hardware changes
    [baseplate.ipt, baseplate.stl, extrusion_clip.ipt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]
2019-04-15 Added mixer density databse and proximity sensor functionality
2019-04-15 Schematic images added
2019-04-15 Added gerber files

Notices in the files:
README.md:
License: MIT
